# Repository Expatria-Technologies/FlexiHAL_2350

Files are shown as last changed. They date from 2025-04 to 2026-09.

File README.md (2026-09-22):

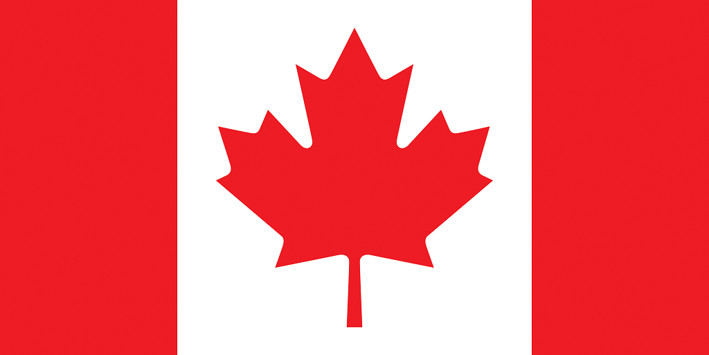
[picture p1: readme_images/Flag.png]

### Canadian-designed open source hardware. For everyone.

# FlexiHAL 2350 CNC Controller
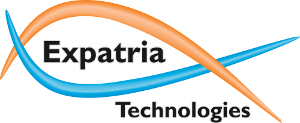
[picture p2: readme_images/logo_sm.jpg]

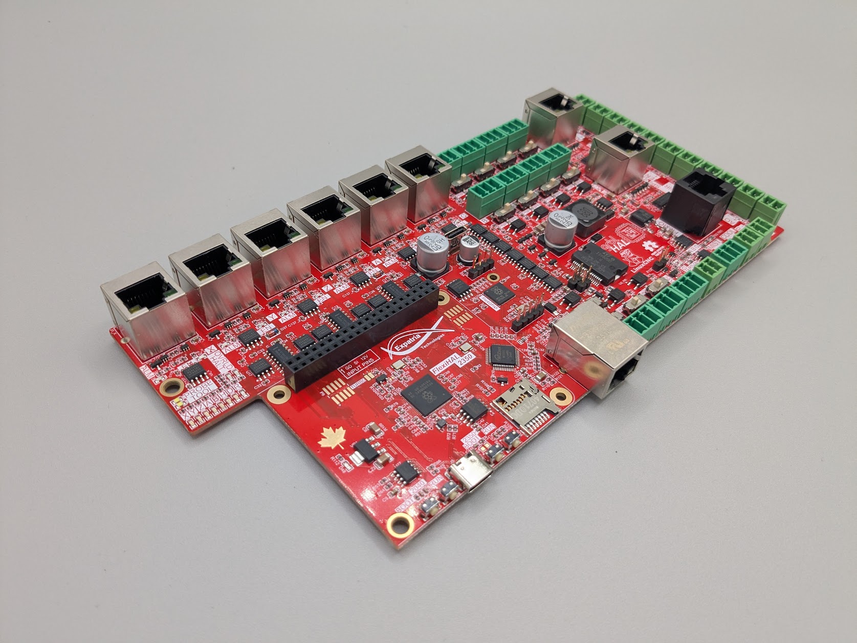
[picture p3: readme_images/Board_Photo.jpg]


Expatria Technologies GRBLHAL and LinuxCNC (and more!) CNC control board

Currently available in our online store:

[https://expatria.myshopify.com/products/flexi-hal-2350](https://expatria.myshopify.com/products/flexihal-2350-cnc-controller-rev-a3-1-for-grblhal-and-linuxcnc)

Please consider buying a board to support our open-source designs. 

The FlexiHal 2350 is designed to be an EMI resistant IO platform for any microcontroller based CNC/motion control firmware or software.  This board includes a few features that we couldn't find on other boards, and it reduces the amount of extra wiring in our setups.  In the co-operative spirit of the PrintNC and other CNC communities, and Open Source Hardware, the FlexiHAL will be licensed and free to use by all parties, including commercial parties, under the CERN-OHL-S V2 license.  It is our hope that the community finds the design useful and that it may be carried forward to help advance the PrintNC and broader CNC hobby community.

The FlexiHAL 2350 is a premium controller that utilizes Raspberry Pi's RP2350 microcontroller.  The RP2350 is well suited for CNC applications using step/direction or quadrature outputs when leveraging the unique capabilities of the PIO cores.    In addition, the Flexi-HAL is intended to be used with the Expatria Real-Time jog controller or similar peripheral:

https://github.com/Expatria-Technologies/RT_Jog_Controller

The key features of the FlexiHAL 2350:

1) 6 Axis of isolated step/dir motor control featuring high-speed digital isolators and differential signal drivers for maximum signal integrity and step rates.
2) 15 general inputs (user+limits+ 2 encoders)
3) 40 points of I/O not including step/dir
4) Integrated support for 3 wire inductive type powered switches.
5) Onboard 5V power regulator.
6) Integrated RS485 with automatic direction control.
7) Support for closed loop stepper motors and servos with alarm feedback.   6 discrete inputs for motor alarm.  6 discrete outputs for motor enable.
8) Two Differential interfaces for a spindle encoder inputs or can be used for general purpose inputs.
9) Real-time control port for remote pendants.
10) Raspberry Pi GPIO connector allows integration of sender software and allows the board to host a full LinuxCNC installation.
11) 5V PWM laser control.  4 additional high-speed 5V outputs.
12) Flood/Mist/Spindle relay drivers.
13) Additional auxilliary relay driver outputs.  8 high-current outputs total.
14) All machine facing IO is galvanically isolated from the MCU and user interfaces.
15) Easy reliable USB-C connection to a PC
16) GRBLHAL Ethernet Websockets or Telnet communication through onboard Ethernet.
17) GRBLHAL SD card G-Code streaming and macro/subroutine storage (including looping and conditional execution) with onboard storage and SD card.

Prebuilt Raspberry Pi LinuxCNC image is located here:  
https://github.com/Expatria-Technologies/Flexi-Pi/releases

Accessory Encoder Breakout PCB is located here:  
[https://github.com/Expatria-Technologies/EST_Accessory_PCB/ENCODER_BREAKOUT_MK2](https://github.com/Expatria-Technologies/EST_Accessory_PCB/tree/main/ENCODER_BREAKOUT_MK2)

Various community mods and accessories are located here:  
https://github.com/Expatria-Technologies/Mods-Accessories

Recommended GRBLHAL Post Processor is here:  
https://github.com/Dietz0r/grblHAL_Fusion360_Post_Processor

## Flexi-HAL Overview

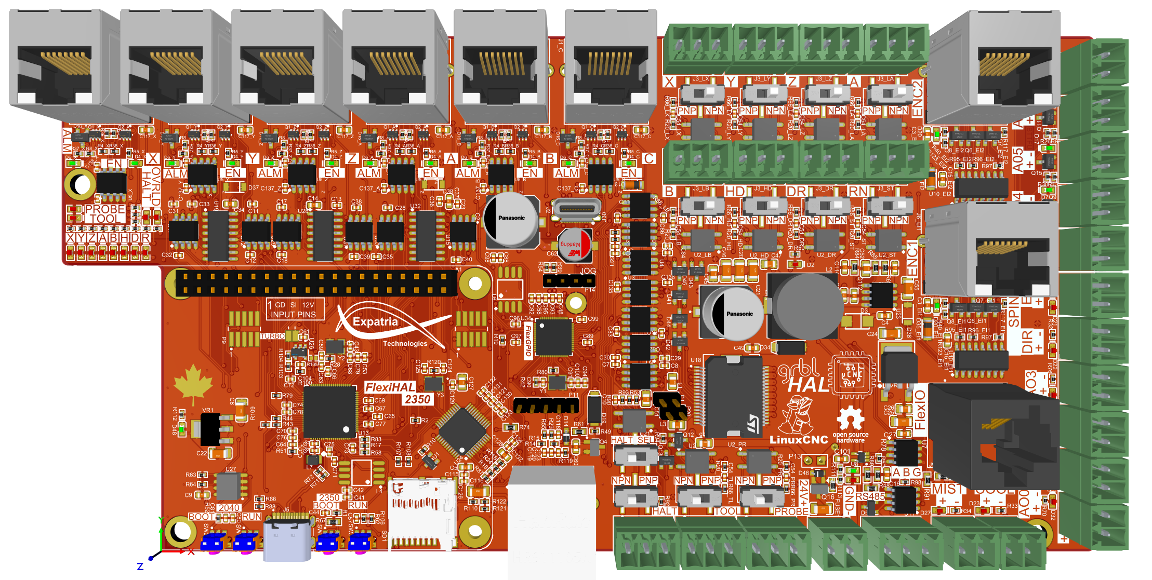
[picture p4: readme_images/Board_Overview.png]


### Pinout List:
This diagram shows which pins connect directly to the RP2350 and which are connected to the RP2040 FlexiGPIO expander.
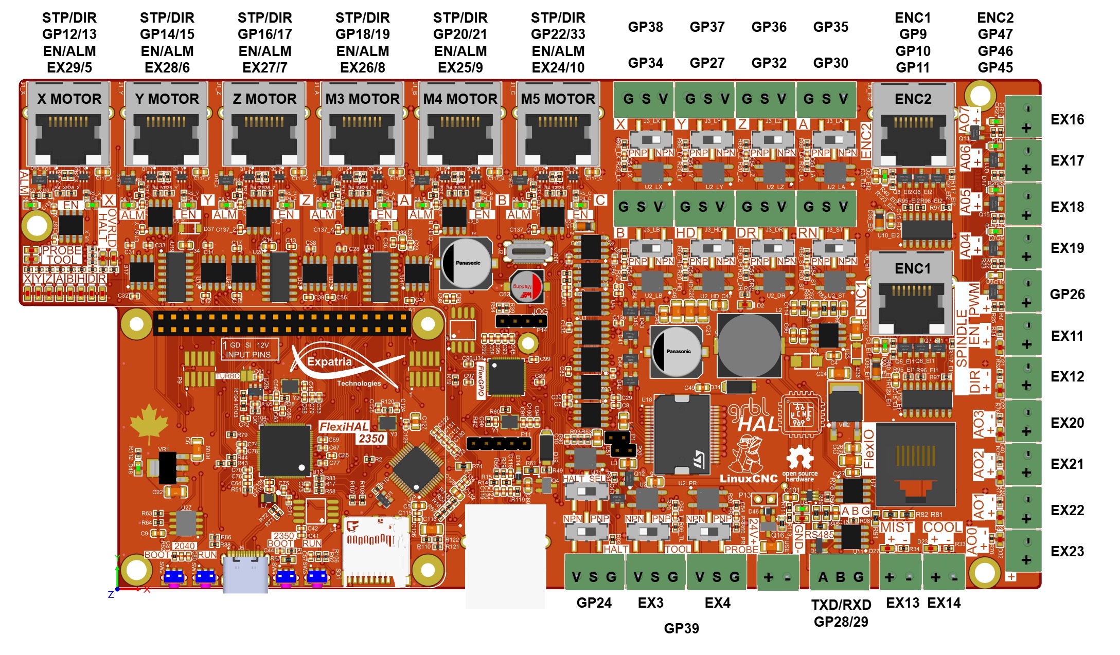
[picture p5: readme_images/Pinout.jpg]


### RP2350 Microcontroller and RP2040 FlexGPIO expander.
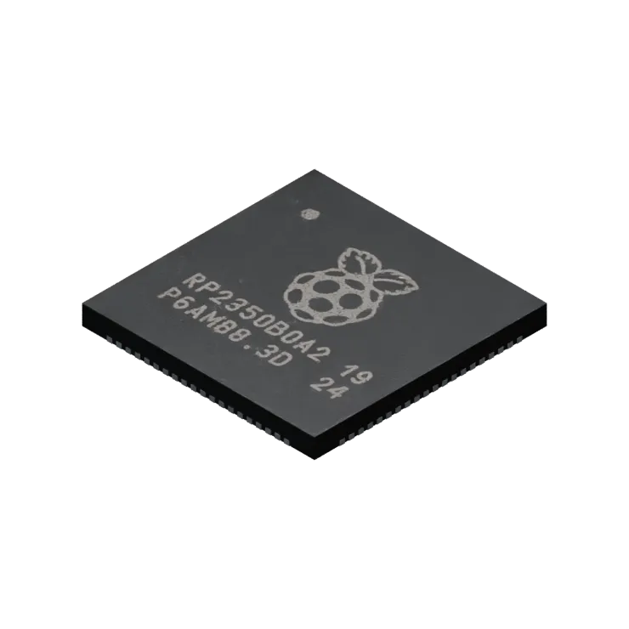
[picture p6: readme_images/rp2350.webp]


The FlexiHAL2350 is built around the RP2350 from Raspberry Pi, an MCU we're genuinely excited about, for its versatile PIO cores and the unique capabilities they unlock.
The board is designed with flexibility at its core, supporting both GRBLHAL and LinuxCNC. In the future we would also like to add support for uCNC.  Pre-built binary firmware for a variety of axis configurations will be made available on the Expatria GitHub, so you can get up and running quickly without compiling from scratch.
For LinuxCNC users, there is a customized port of the Remora project alongside FlexiHAL, making it straightforward to switch between motion control environments. In this mode a Raspberry Pi 5 is recommended when running the Expatria Flexi-Pi image.

In order to expand the amount of I/O available on the board, a custom I2C GPIO expander is implemented on an additional RP2040 MCU.  This allows for a large number of additional IO points with much greater potential flexibility than is offered by traditional GPIO expanders.  It will be possible to implment functions such as additional analog/PWM outputs, nexopixel outputs and additional stepper outputs by extending the FlexiGPIO code.

FlexGPIO source code is posted here:  
[https://github.com/Expatria-Technologies/FlexGPIO](https://github.com/Expatria-Technologies/FlexGPIO)

FlexGPIO GRBLHAL plugin is posted here:  
[https://github.com/Expatria-Technologies/plugin_FlexGPIO](https://github.com/Expatria-Technologies/plugin_FlexGPIO)

### UF2 Bootloader
The FlexiHAL 2350 uses the RP2350's built-in UF2 bootloader. This allows you to upgrade or change the firmware on the flexi as easily as copying a file to a USB drive.  Pre-built binary firmwares from Expatria are distributed as UF2 files.  To enter UF2 mode hold the BOOT button while powering up the board or while pulsing the RUN button.  Note that there are bootloader buttons for both the RP2040 based FlexGPIO expander as well as the main RP2350 processor.

Once in bootloader mode, the Flexi will appear as a USB storage device called "RPI-RP2."  Simply copy the new firwmare to this USB drive and the board will automatically install it and reboot.  Some operating systems may give an error when flashing is complete because the 'disk' was removed without ejecting it.  This error can be ignored.

### Power Input
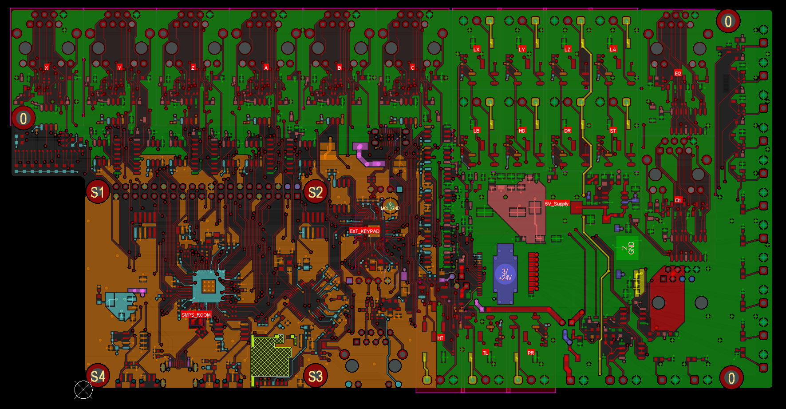
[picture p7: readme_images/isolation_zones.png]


The Flexi-HAL features the capability for full power and ground isolation between the sensitive microncontroller and host circuits, and the external IO that extends out to the rest of the machine.  There is a single input for 12-24VDC.  The board has its own onboard 5V regulator to power the stepper drivers and external RS485 interface.  There is also a small capacity 12V LDO that is specifically for driving the limit and user switches.

Flexi-HAL has reverse polarity as well as over-current protection beyond 1.75A.  This is important to consider when using external relays that draw a lot of current as this may overwhelm the capacity of the board.  If you need to drive more than 250 mA through the auxillary and mist/coolant relay outputs, external relays are likely required.

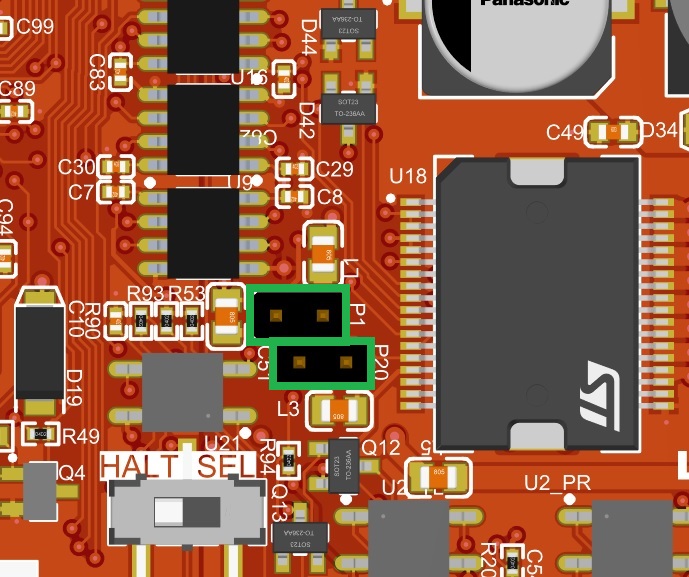
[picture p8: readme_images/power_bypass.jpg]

Normally the MCU and RPI header will be powered via the USBC connector.  The RT control interface is also powered from the isolated domain.  By installing two jumpers on the above offset pins, the 5V power and ground isolation can be bypassed and the Flexi-HAL will operate without an external 5V supply in a semi-isolated state.  This does reduce the EMI resistance of the board and is not recommended when sending Gcode via the USBC connector.

Note: With the isolation jumpers not-populatd, and the Flexi-HAL connected to 12-24v power, it may appear that the board is ready to run as some LEDs illuminate. You MUST provide 5v power to the isolated domain (MCU, Jogger) either through USB or the bypass jumpers in order for the MCU and Jogger to turn on.

### Stepper Drivers
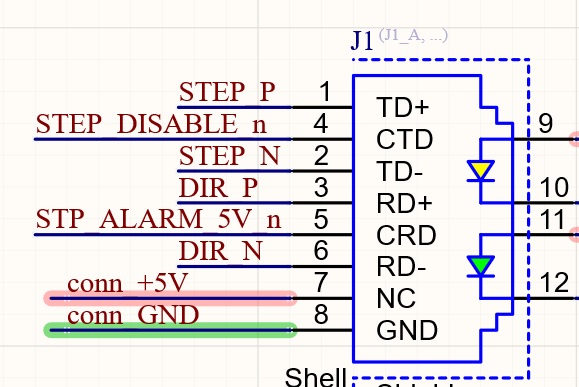
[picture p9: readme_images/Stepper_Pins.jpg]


The stepper drivers are designed to be used with standard or flex rated RJ45 cables.  Unfortunately you will need to ensure that at the external driver the high and low signal pairs are connected correctly as there is no standard pinout on these drivers.  The 8 pin connection allows you to run a high and low pair for every signal to ensure the best possible signal integrity.  The Flexi-HAL uses high speed digital isolators and differential RS-422 style signal drivers for the motion signals.

Dedicated enable and alarm inputs are routed through the FlexGPIO expander.  A specific motor alarm interrupt is provided to immediately notify the host processor.  Alarm and enable can be set to any polarity that is required for operation.  There are LEDs provided on the board for every motor signal to help with debugging wiring issues.

Typical wiring for most open-loop stepper drivers: 



### Auxillary Outputs
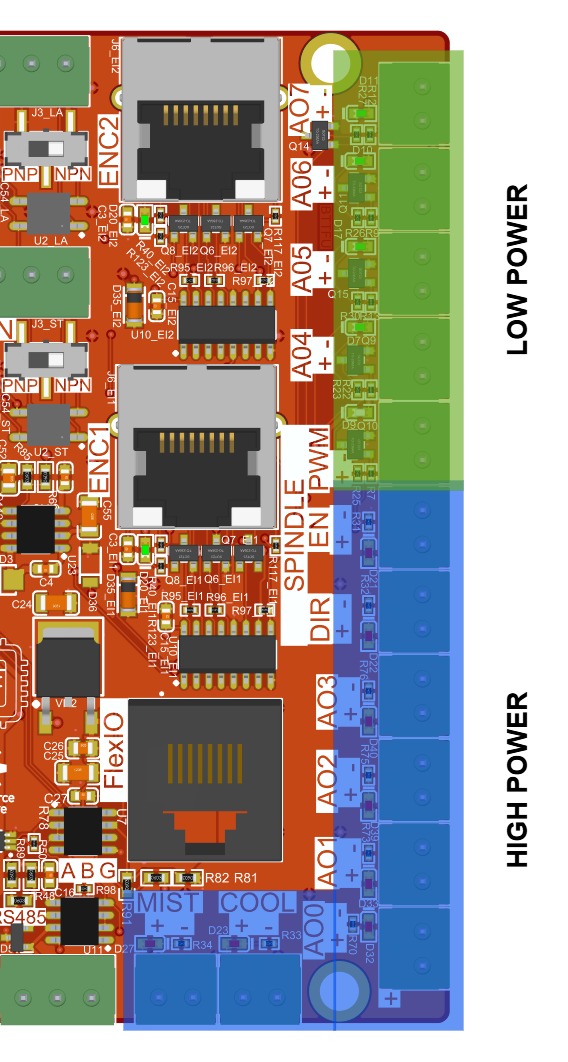
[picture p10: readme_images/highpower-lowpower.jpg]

Two style of outputs are provided: high power and low power.  High power outputs are driven directly from the board input power (12-24V).  Low power outputs are driven at 5V.  All outputs are PNP style high-side switching.

#### High Power Outputs
Any single high-power output can drive up to 700 mA, though the total current supplied by the board is a maximum of 1.75A.  Each automotive grade output has short circuit, over-current and thermal shutdown protection.

#### Low Power Outputs
The low power outputs are designed for fast switching applications such as PWM output, neopixels or even additional stepgens.  They should not be configured to drive more than 10 mA.  They are provided with limited over-voltage and short-circuit protection.

### PWM Spindle Control

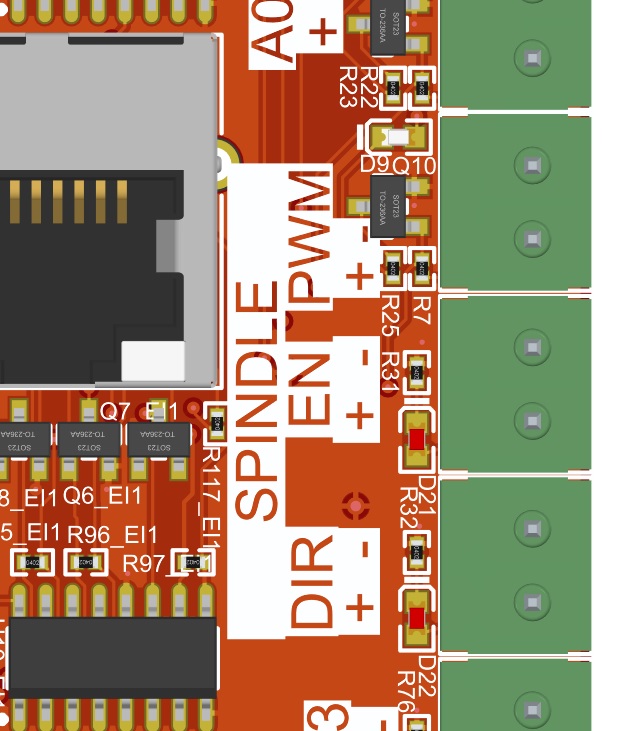
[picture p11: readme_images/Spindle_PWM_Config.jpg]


The spindle PWM pin is directly connected to the RP2350 main MCU.  This is normally used to drive a laser module with pulse modulation.  To use this output with a 0-10V analog spindle control, an external PWM converter must be used.

### RS485 Spindle Control
This interface is primarily intended to be used with a Huanyang style VFD for spindle control.  The A, B and G (common) pins are marked on the top and bottoms sides of the PCB.  Simply connect the appropriate pins to the terminals on the VFD.  Note that the G pin should be used for signal common, it should not be connected to the shield of a shielded cable.

https://github.com/grblHAL/Plugins_spindle/

### 6 Axis limit and auxillary inputs

A total of 9 direct 3 wire opto-coupled inputs are provided to cover limit and auxillary inputs.  Both PNP and NPN switches are supported.  A selector switch is provided on each input.

Auto-squaring is supported by enabling ganged axes in GRBLHAL and setting the appropriate pins.

In addition two probe inputs are provided that are connected to the FlexGPIO with a dedicated interrupt signal.  Polarity and enable masks are fully configurable.

### HALT Input signal and Polarity Selection

The HALT signal is not a safety feature and should not be used in place of a true electrical emergerncy stop.  It is intended to notify the controller of urgent requests.  The halt signal is shared between the PCB terminal and the RT control interface, but the polarity and operation is freely configurable between NPN, PNP, NO and NC.

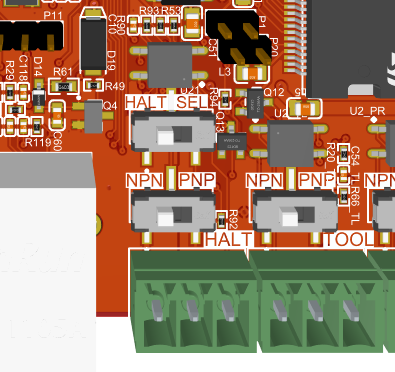
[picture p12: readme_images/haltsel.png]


If you are in doubt of the correct header position for your case, you may simply try both positions and choose the one where the HALT signal is not asserted (red light is not on) when in the nominal operating condition.

### Real-Time Control Port
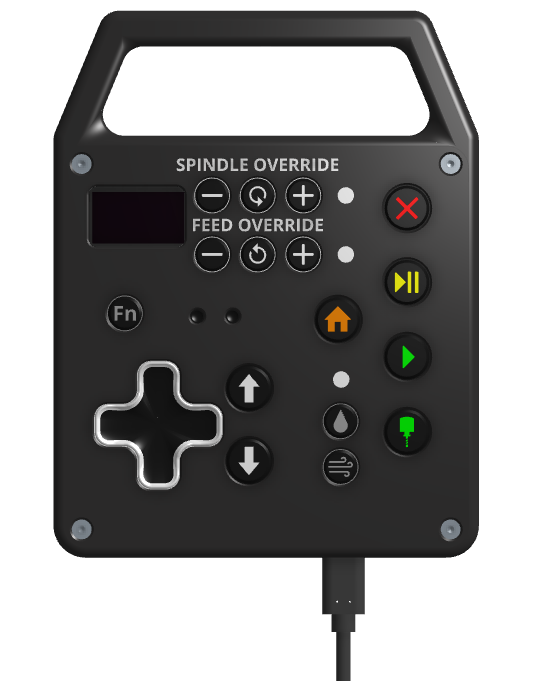
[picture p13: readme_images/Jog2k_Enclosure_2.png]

This port is intended to allow for external pendant type devices to issue real-time jogging and override controls to the motion  controller.  It uses I2C signalling and adds additional signals for the keypad interrupt as well as the Halt signal.  We feel that a robust and wired control is the safest way to interact with a CNC machine in real time.  A simple reference controller implementation is under active development, but there are some additional code examples referenced in the GRBLHAL I2C keypad plugin repository:

https://github.com/grblHAL/Plugin_I2C_keypad/

https://github.com/Expatria-Technologies/RT_Jog_Controller/

### Encoder Input Ports
The two encoder ports are used in either of two ways.  First, these ports allow a differential connection to an external encoder for a robust GRBLHAL lathe implementation or to support a high-speed encoder input for LinuxCNC.  An encoder such as E6B2-CWZ1X is suitable for most spindle applications.  Additionally, an encoder based isolated ADC module can be used for Plasma THC applications.

The RJ45 pinout:  
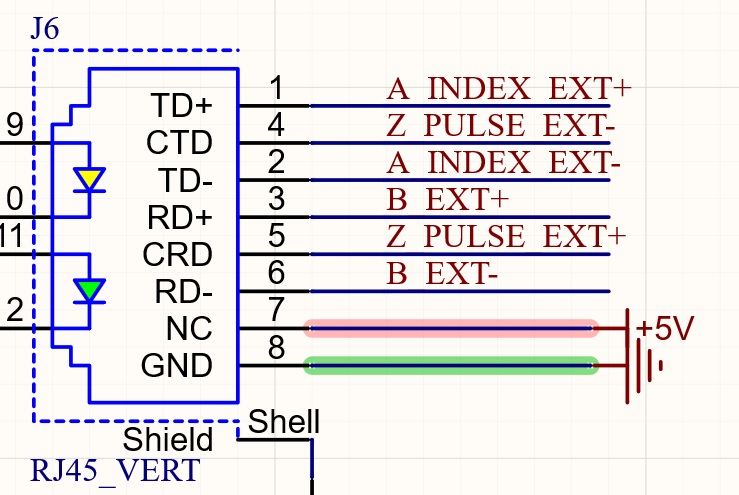
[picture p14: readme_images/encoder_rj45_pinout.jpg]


There is also a small breakout available that exposes these signals for use as discrete opto-coupled inputs.  This can be useful when you have a group of signals that are remotely co-located (such as the sensors in an ATC spindle) so that you only need to bring one cable back to the mainboard.

Encoder Breakout Board:  
[https://github.com/Expatria-Technologies/EST_Accessory_PCB/tree/main/ENCODER_BREAKOUT_MK2](https://github.com/Expatria-Technologies/EST_Accessory_PCB/tree/main/ENCODER_BREAKOUT_MK2)
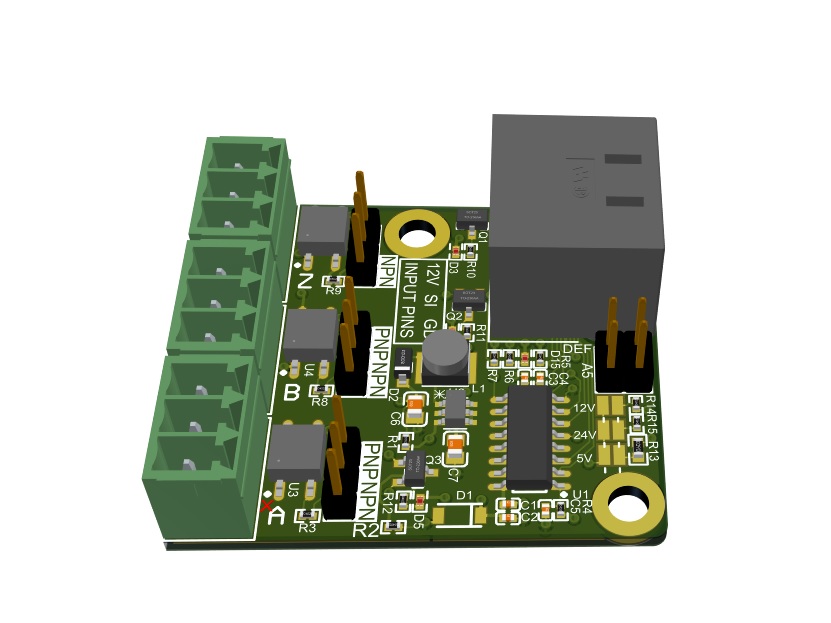
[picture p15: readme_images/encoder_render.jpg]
  

### FlexIO Port
The FlexiHAL2350 introduces a new type of expansion port for Expatria.  The FlexIO port multiplexes the RS485 interface independently to a second connector that carries both power and RS485 signals.  This can be used as both a power source for external modules that are powered from the FlexiHAL's 24V input, or it can serve as a power supply for the board.  The RS485 signalling can be used with Modbus server devices such as the PicoHAL running the nanoModbus GRBLHAL plugin to provide independent control of toolchanges, LEDs, fans etc.

The RJ45 pinout:  
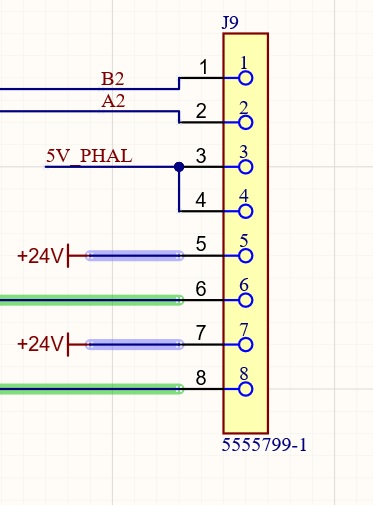
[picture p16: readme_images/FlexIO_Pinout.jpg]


Details on the PicoHAL are posted here:  
[https://github.com/Expatria-Technologies/PicoHAL_HW](https://github.com/Expatria-Technologies/PicoHAL_HW)

NanoModbus GRBLHAL Plugin is posted here:  
[https://github.com/Expatria-Technologies/grblhal_nmbs_plugin](https://github.com/Expatria-Technologies/grblhal_nmbs_plugin)

nanoModbus toolchanger in action; also showing Sienci's ATCI plugin.  In this video, the LEDs and all motions of the tool carousel are controlled via RS485 Modbus.

https://github.com/user-attachments/assets/e5c6b0d1-849d-4eac-88a9-3914cdb023e6

### Raspberry PI expansion header
The Rasberry Pi GPIO header allows the Flexi-HAL to host a full Raspberry Pi type SBC.  This allows the platform to support LinuxCNC via the Remora project.  Power should be connected to either the Pi or to the FlexiHAL, not both.

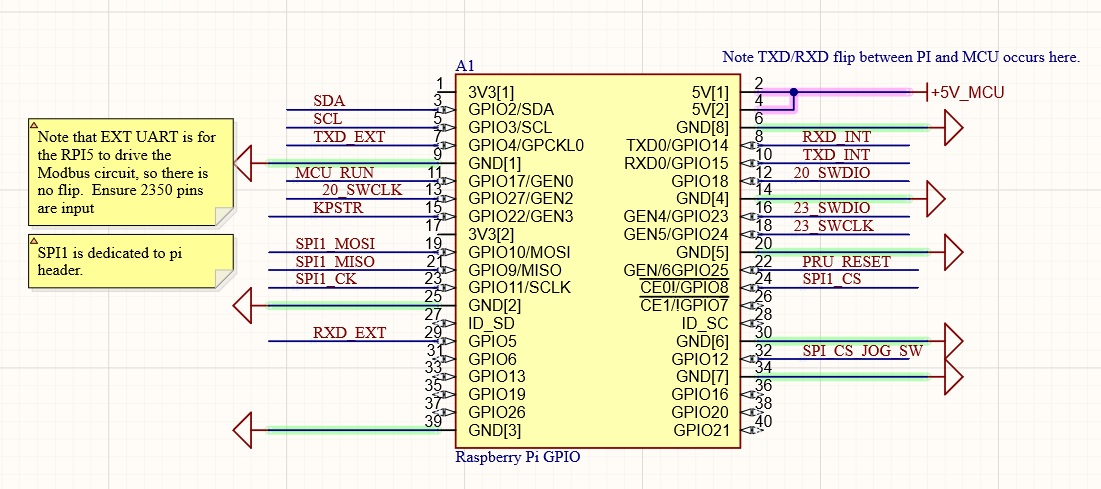
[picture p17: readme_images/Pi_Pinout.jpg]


### Accessories
Some 3D printed accessories are avilable in [Mods & Accessories](https://github.com/Expatria-Technologies/Mods-Accessories/), including a DIN rail mount and enclosures/mounts for the limit and button breakouts.

### Default Jumper Locations
There are no jumpers needed for the operation of this board.  The only jumpers are for the 5V power bypass.

### Example Wiring Diagram
A comprehensive wiring diagram has been developed by the PrintNC community using the FlexiHAL.  While not specific to Flexi, this gives a great example of how to connect the board into the rest of a complete electronics box to drive a CNC machine. 
https://wiki.printnc.info/en/v3/wiring

### Attributions
This project uses components from the very helpful actiBMS library.

https://github.com/actiBMS/JLCSMT_LIB

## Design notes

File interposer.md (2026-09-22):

For the A3 beta release of the FlexiHAL2350, an interposer is necesssary to use LinuxCNC via SPI to a Raspberry Pi 5.  If you purchased a beta board before June 5 2026 and did not receive an interposer, please contact Expatria via the webstore or on Discord and we will send you one.

The interposer doubles as a GPIO extender to allow use of an RPI5 with the OEM heatsink/cooler.  To install the interposer, make sure the white stripe is towards the RPI5 area of the board (pointed at the RP2350) as shown in the images below.

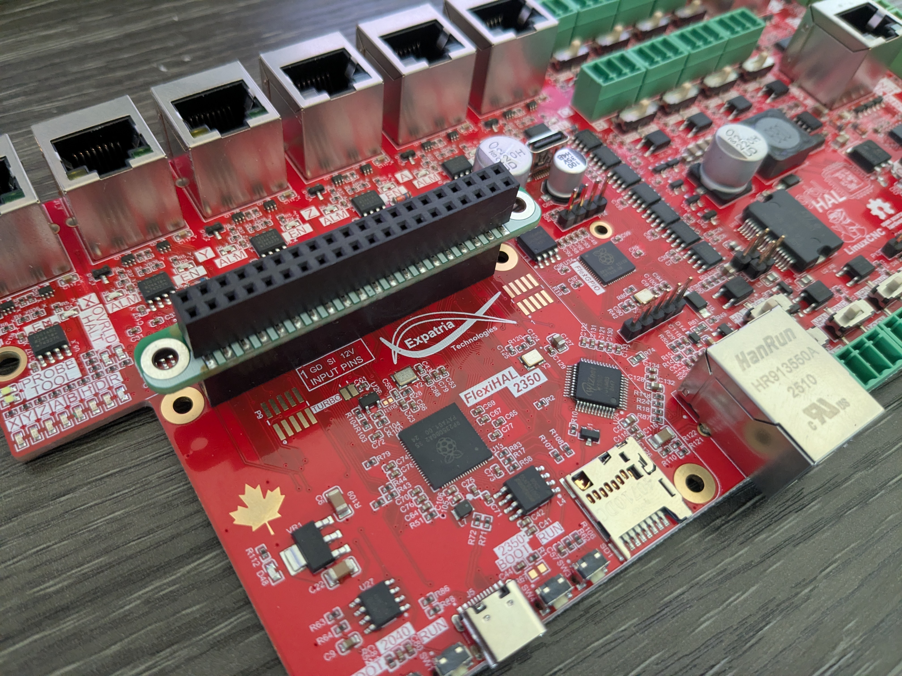
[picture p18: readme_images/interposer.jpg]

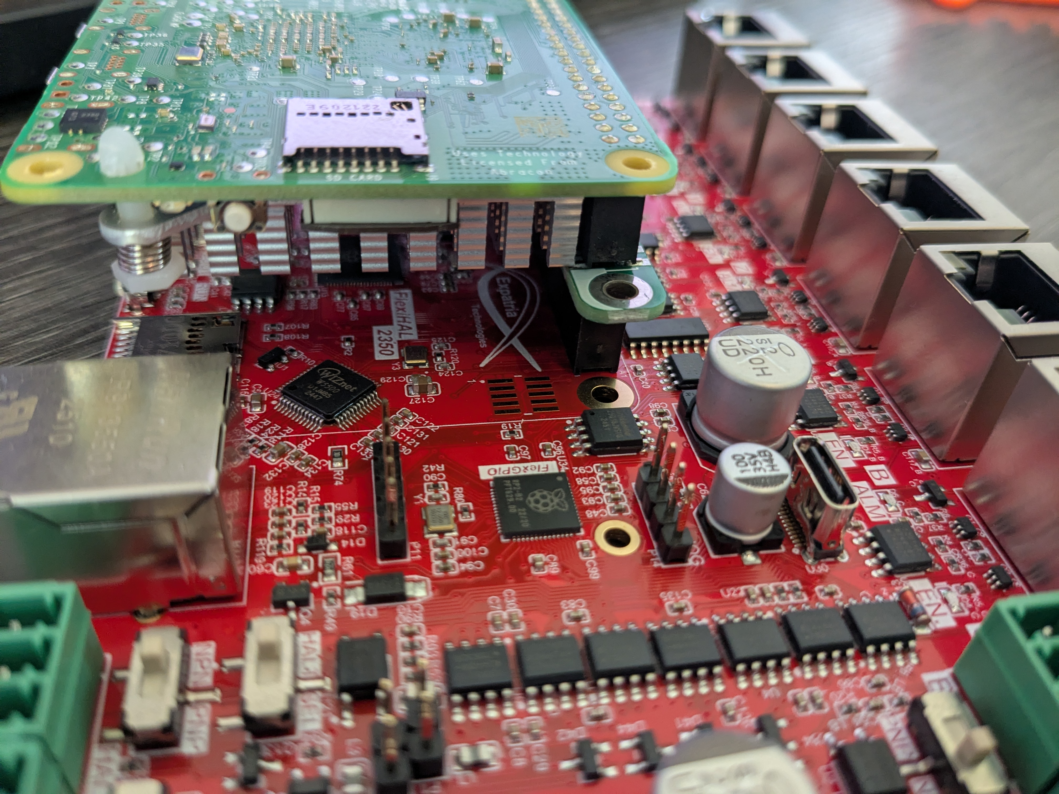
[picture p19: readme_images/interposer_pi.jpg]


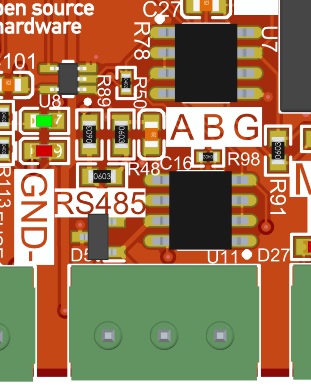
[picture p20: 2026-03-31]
readme_images/RS485_secion.jpg

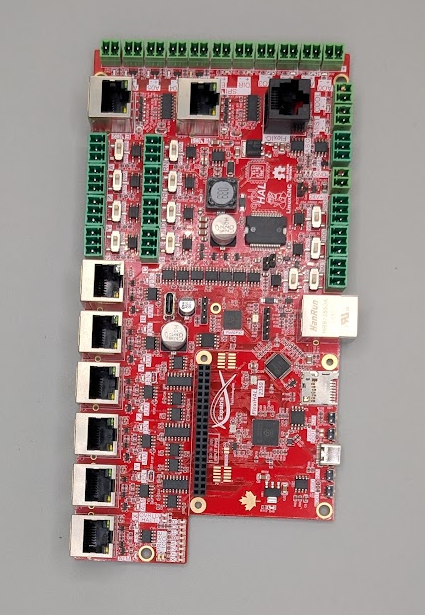
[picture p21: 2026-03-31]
readme_images/board_top.png

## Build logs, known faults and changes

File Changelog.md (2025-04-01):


# Flexi-HAL CNC Controller

## Changelog

### A4 Revision

- Initial Release

### A5 Revision
- Added HALT signal polarity selection.
- Modified RS485 UART isolation for better compatibility with more VFDs under LinuxCNC.
- Added jumper resistor option to route STP_ALARM signal to B limit switch input.
- Depopoulated isolation bypass headers to prevent magic smoke escape.
- Added termination resistors to encoder input to improve signal integrity.
- Added additional overvoltage protection to external circuits.

- ### A6 Revision
- Fixed silkscreen issue on Probe and Tool ports.
- Updated silkscreen to clarify copyright permissions on Expatria and FlexiHAL names.
- Added solder points to USB nets on top layer.
- Changed encoder routing for better signal integrity.  Pinout is unchanged.

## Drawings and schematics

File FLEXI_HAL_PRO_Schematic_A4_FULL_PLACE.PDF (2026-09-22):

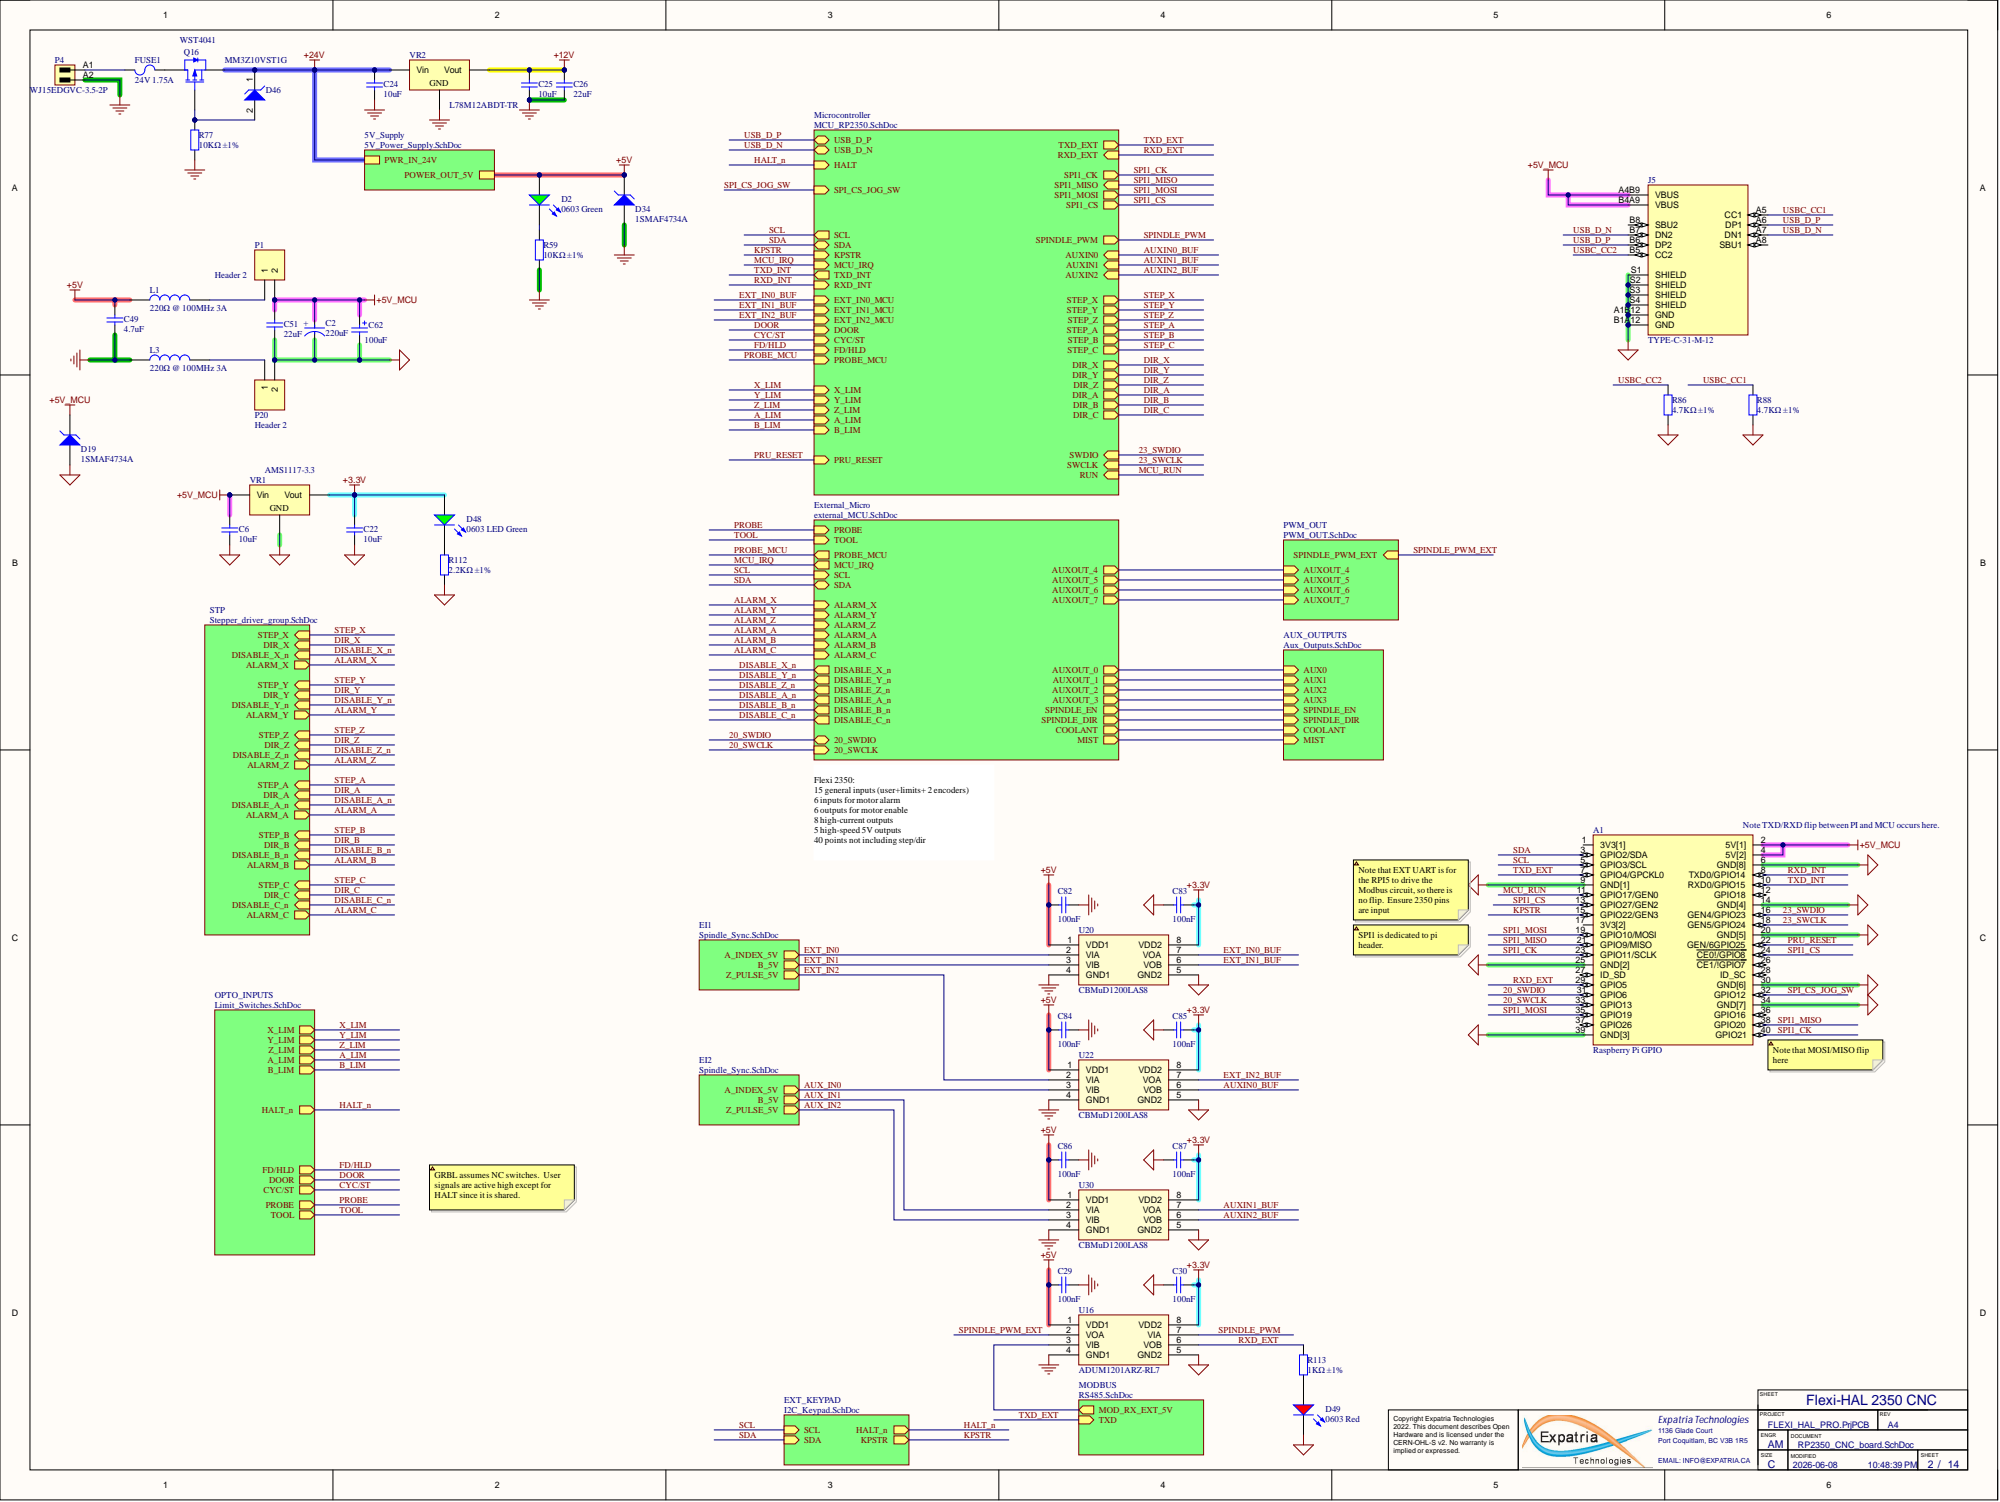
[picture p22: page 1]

hat MOSI/MISO fl

Hardware a n d i s l i c e n s e d u n d er th e CERN-OHL-S v 2. No warra nty i s i m p l i e d or e x pre s s e d . | | P R OJE C T FLEXI_HAL_PRO. P rj P C | R E V A4

B Copyright Expatria Technologies 2022. This document describes Open

E N G R A M | D O C U M E N T RP2350_C N C_board. S c h D o c

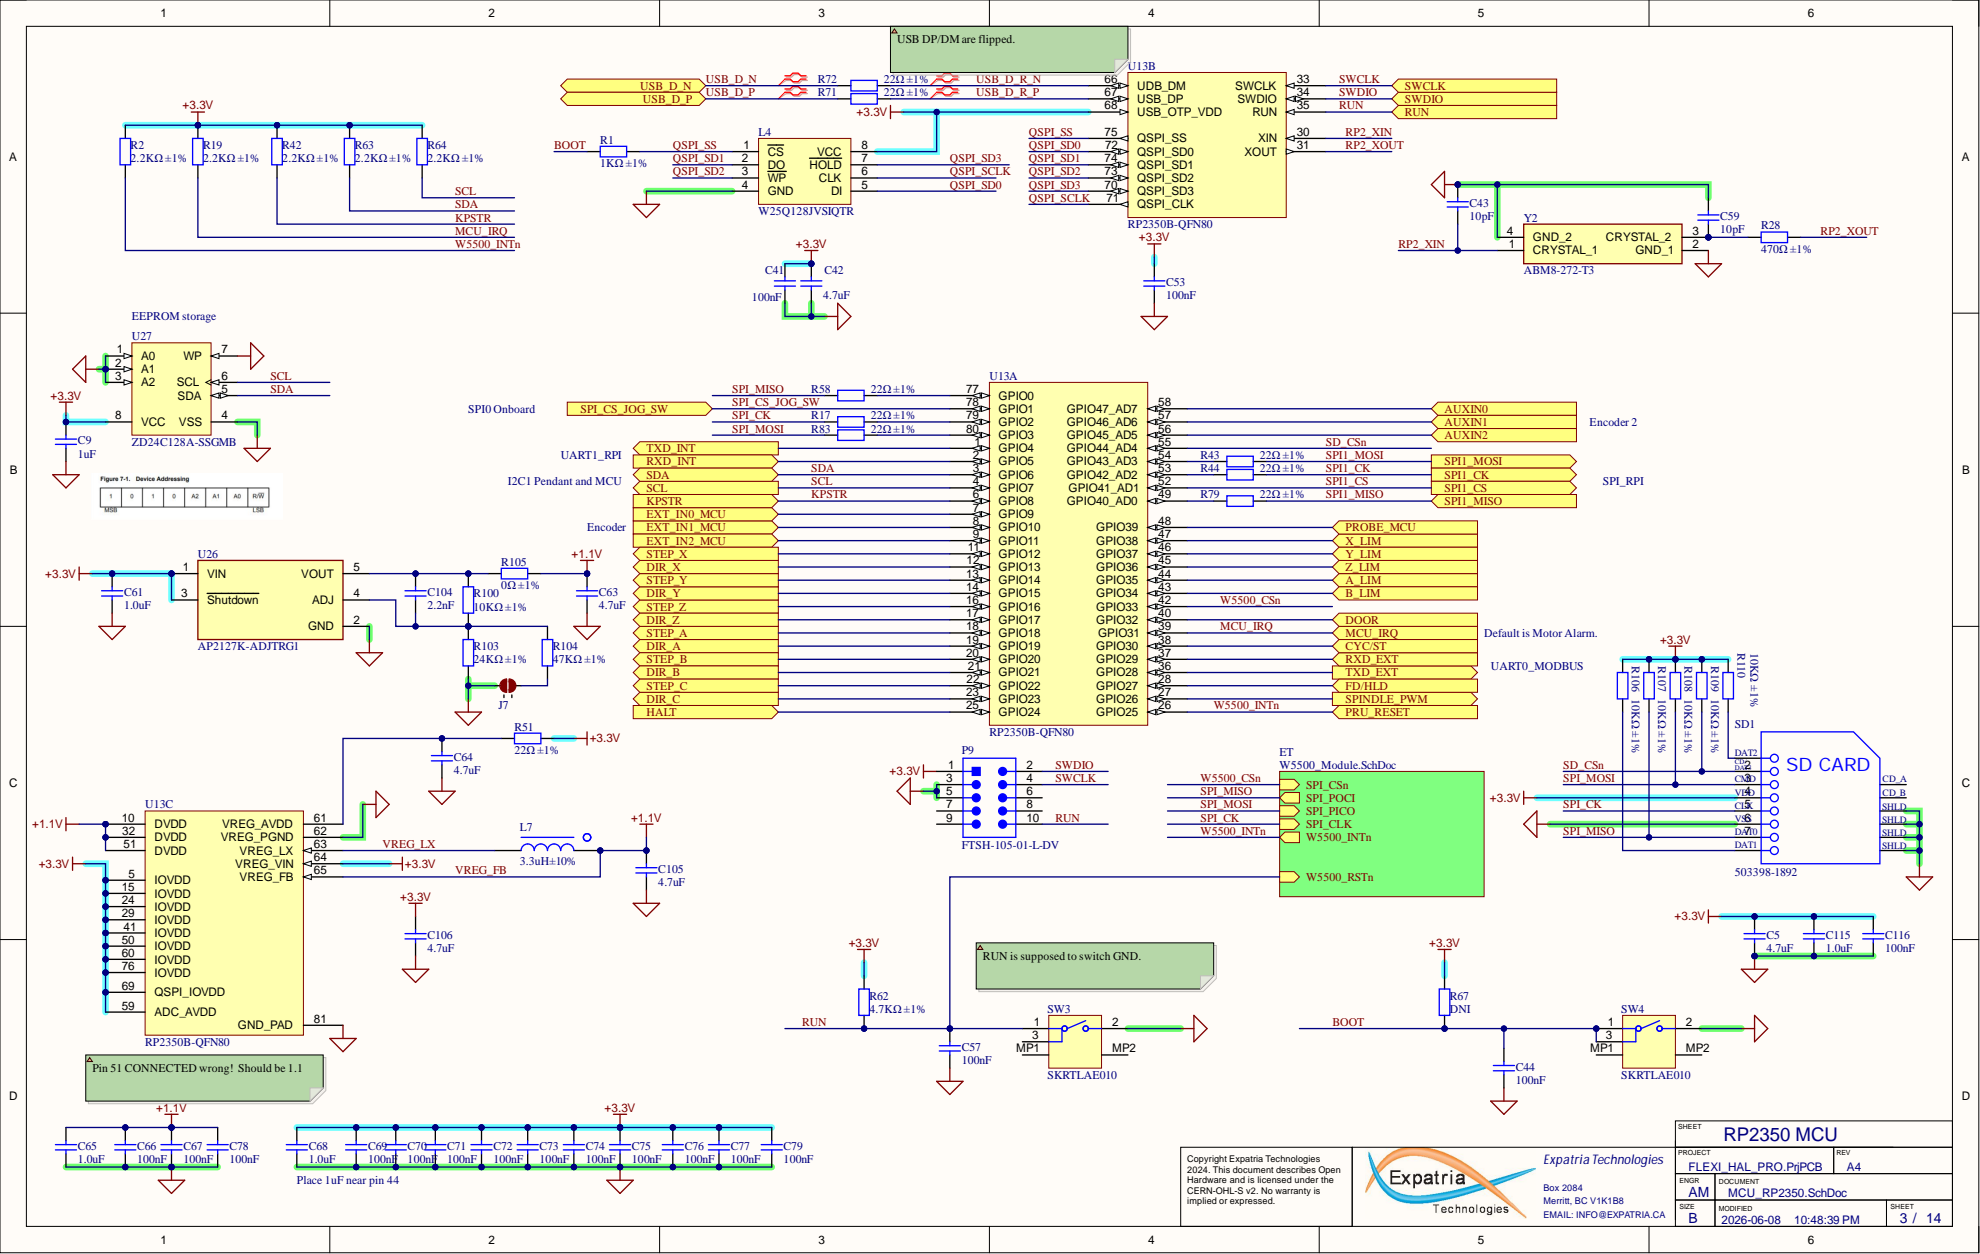
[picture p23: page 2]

USB DP/DM are flipped.

RUN is supposed to switch GND.

Pin 51 CONNECTED wrong! Should be 1.1

Copyright Expatria Technologies 2024. This document describes Open Hardware and is licensed under the CERN-OHL-S v2. No warranty is implied or expressed. | | PROJECT FLEXI_HAL_PRO.PrjPCB | REV

AM ENGR | DOCUMENT MCU_RP2350.SchDoc

Box 2084
Merritt, BC V1K1B8
EMAIL: INFO@EXPATRIA.CA

SIZE B | MODIFIED 2026-06-08 10:48:39 PM | SHEET

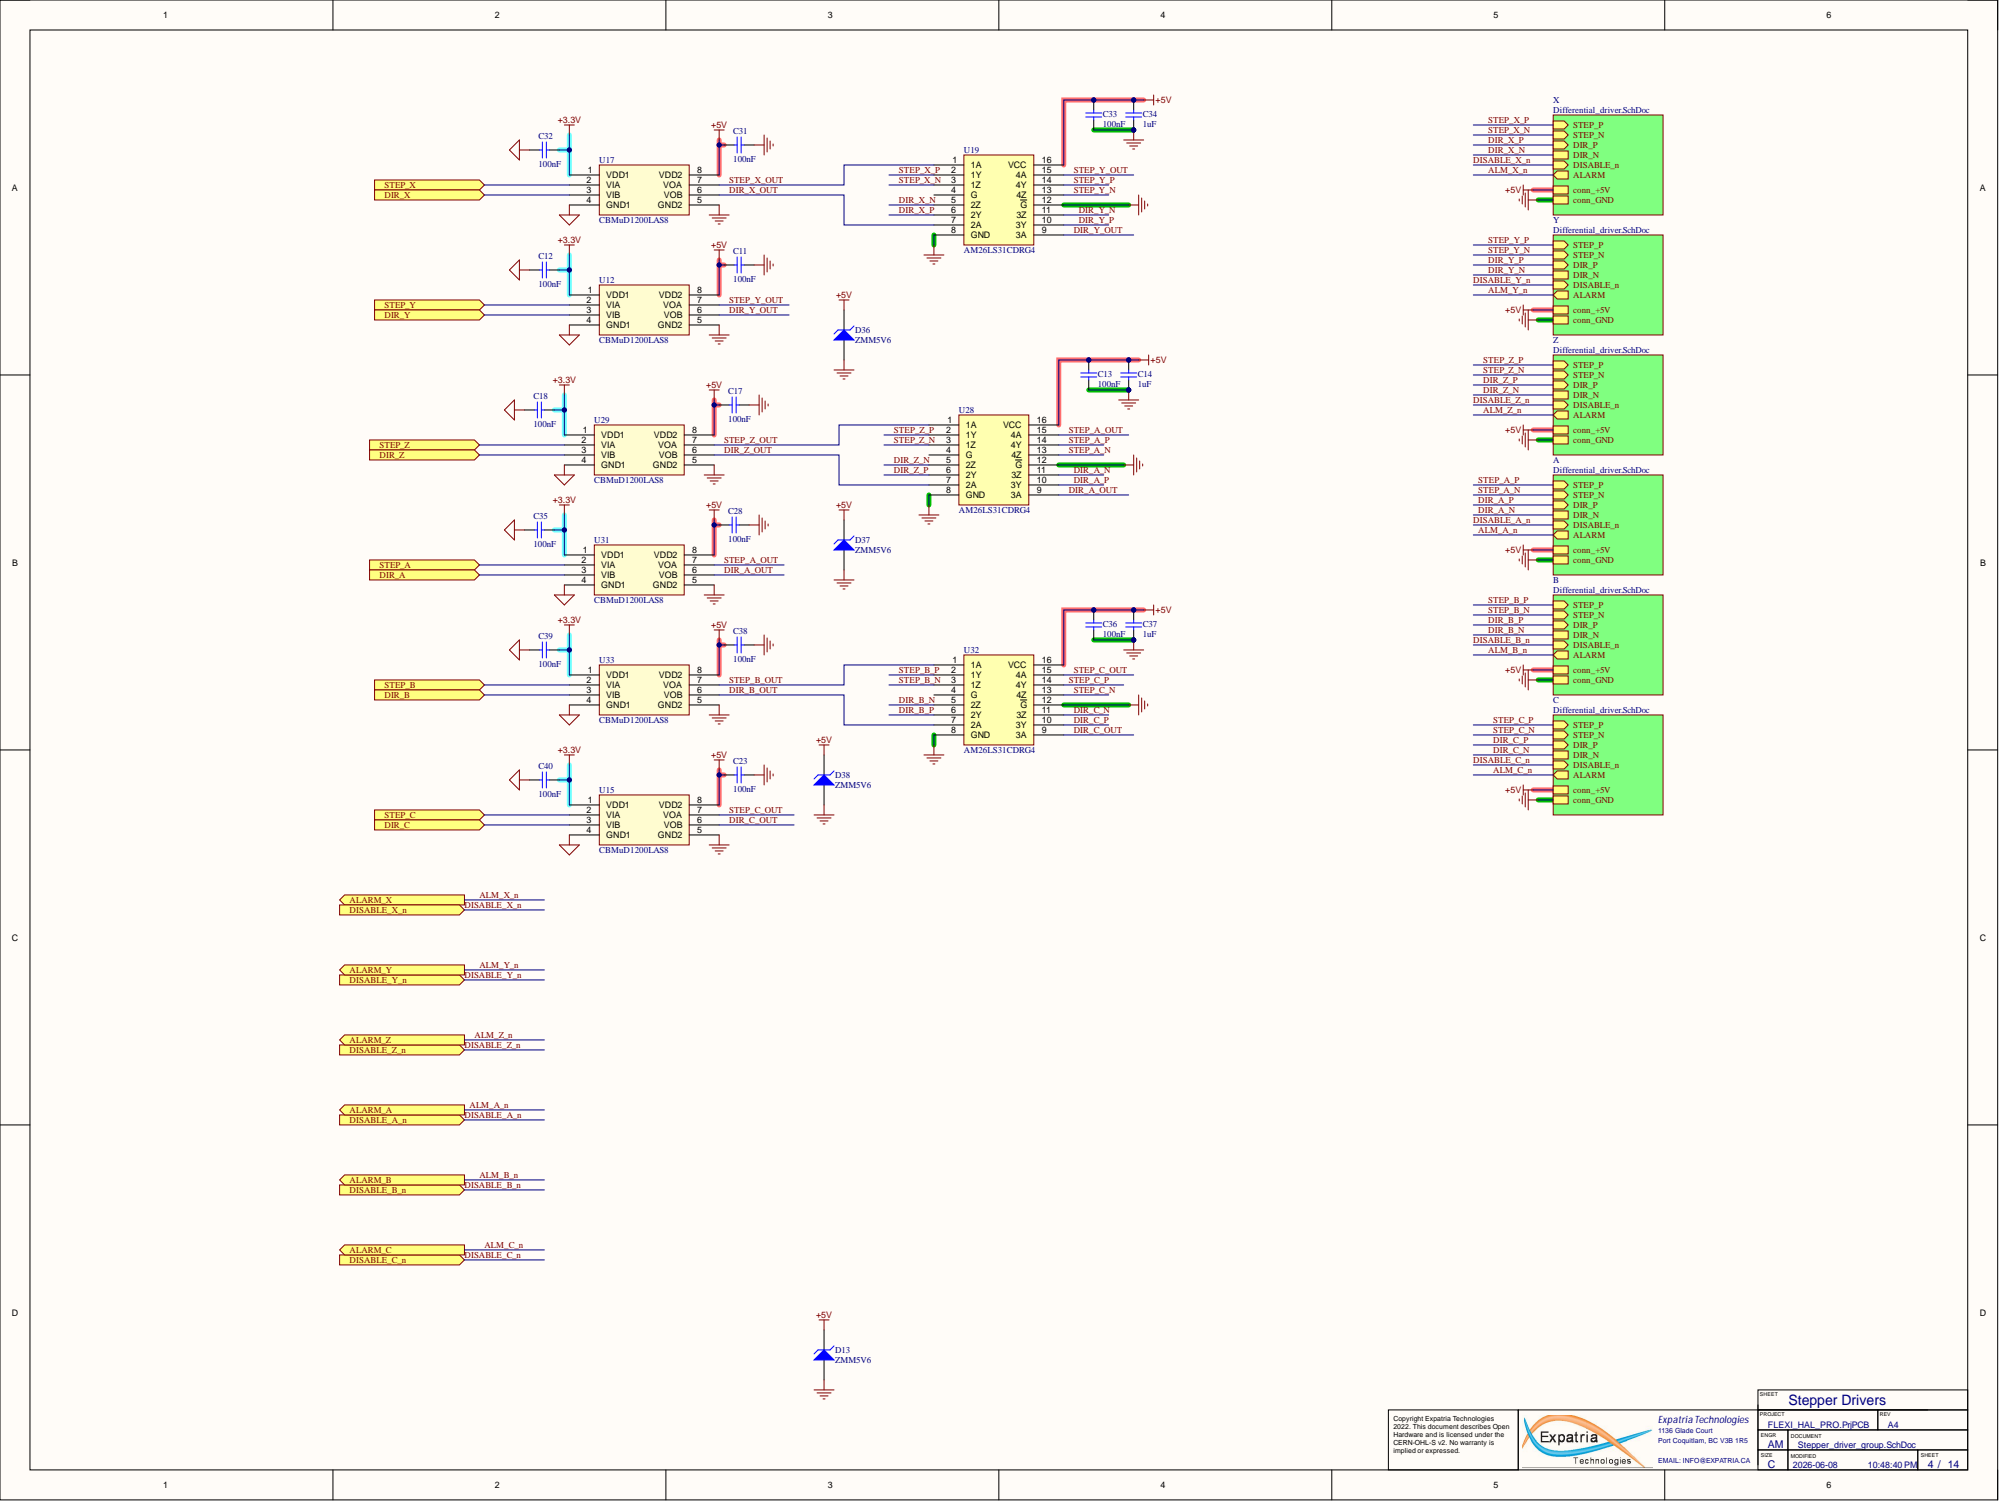
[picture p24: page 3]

FLEXI_HAL_PRO.PrjPCB Copyright Expatria Technologies

ENGR AM | DOCUMENT Stepper_driver_group.SchDoc

implied or expressed.

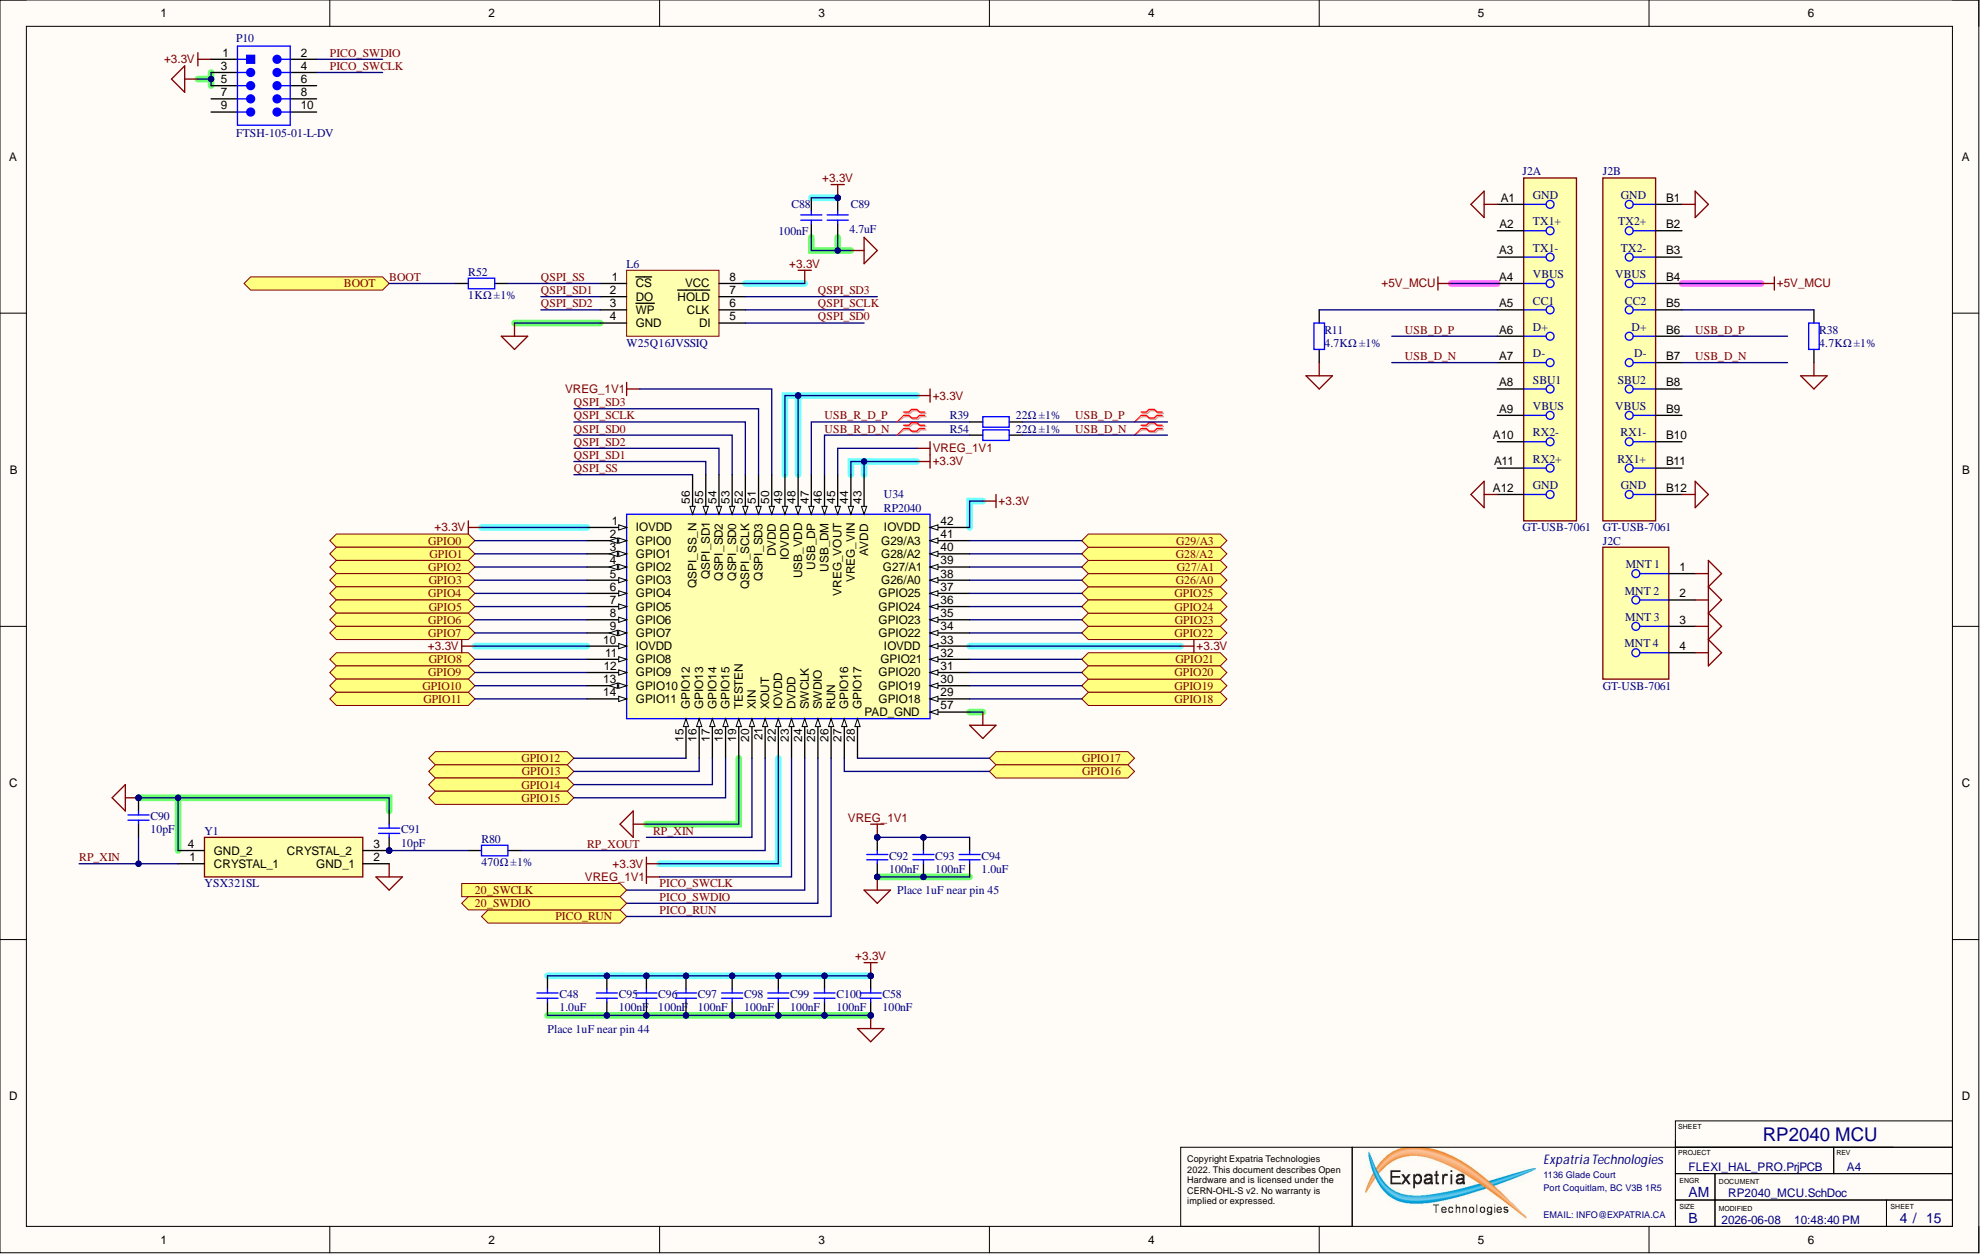
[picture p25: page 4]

QSPI_SD2
QSPI_SD1
QSPI_SS

RP_XOUT R80

RP2040_MCU.SchDoc

RSTn 37 RSVD 38 RSVD 39 RSVD 40 RSVD 41 RSVD 42 PMODE2 43 PMODE1 44 PMODE0 45 NC 46 NC 47 AGND 48

SPDLED 24 LINKLED 25 DUPLED 26 ACTLED 27 VDD 28 GND 29 XI/CLCKIN 30 XO 31 SCSn 32 SCLK 33 MISO 34 MOSI 35 INTn 36

TX_R_P | | TXP 2

AGND 3 | SPI_POCI
AVDD 4

RX_R_P | RXP 6 | XO

DNC 7 | XI

AGND 9
EXRES1 10
AVDD 11 | GRN_LED

W5500_Module.SchDoc

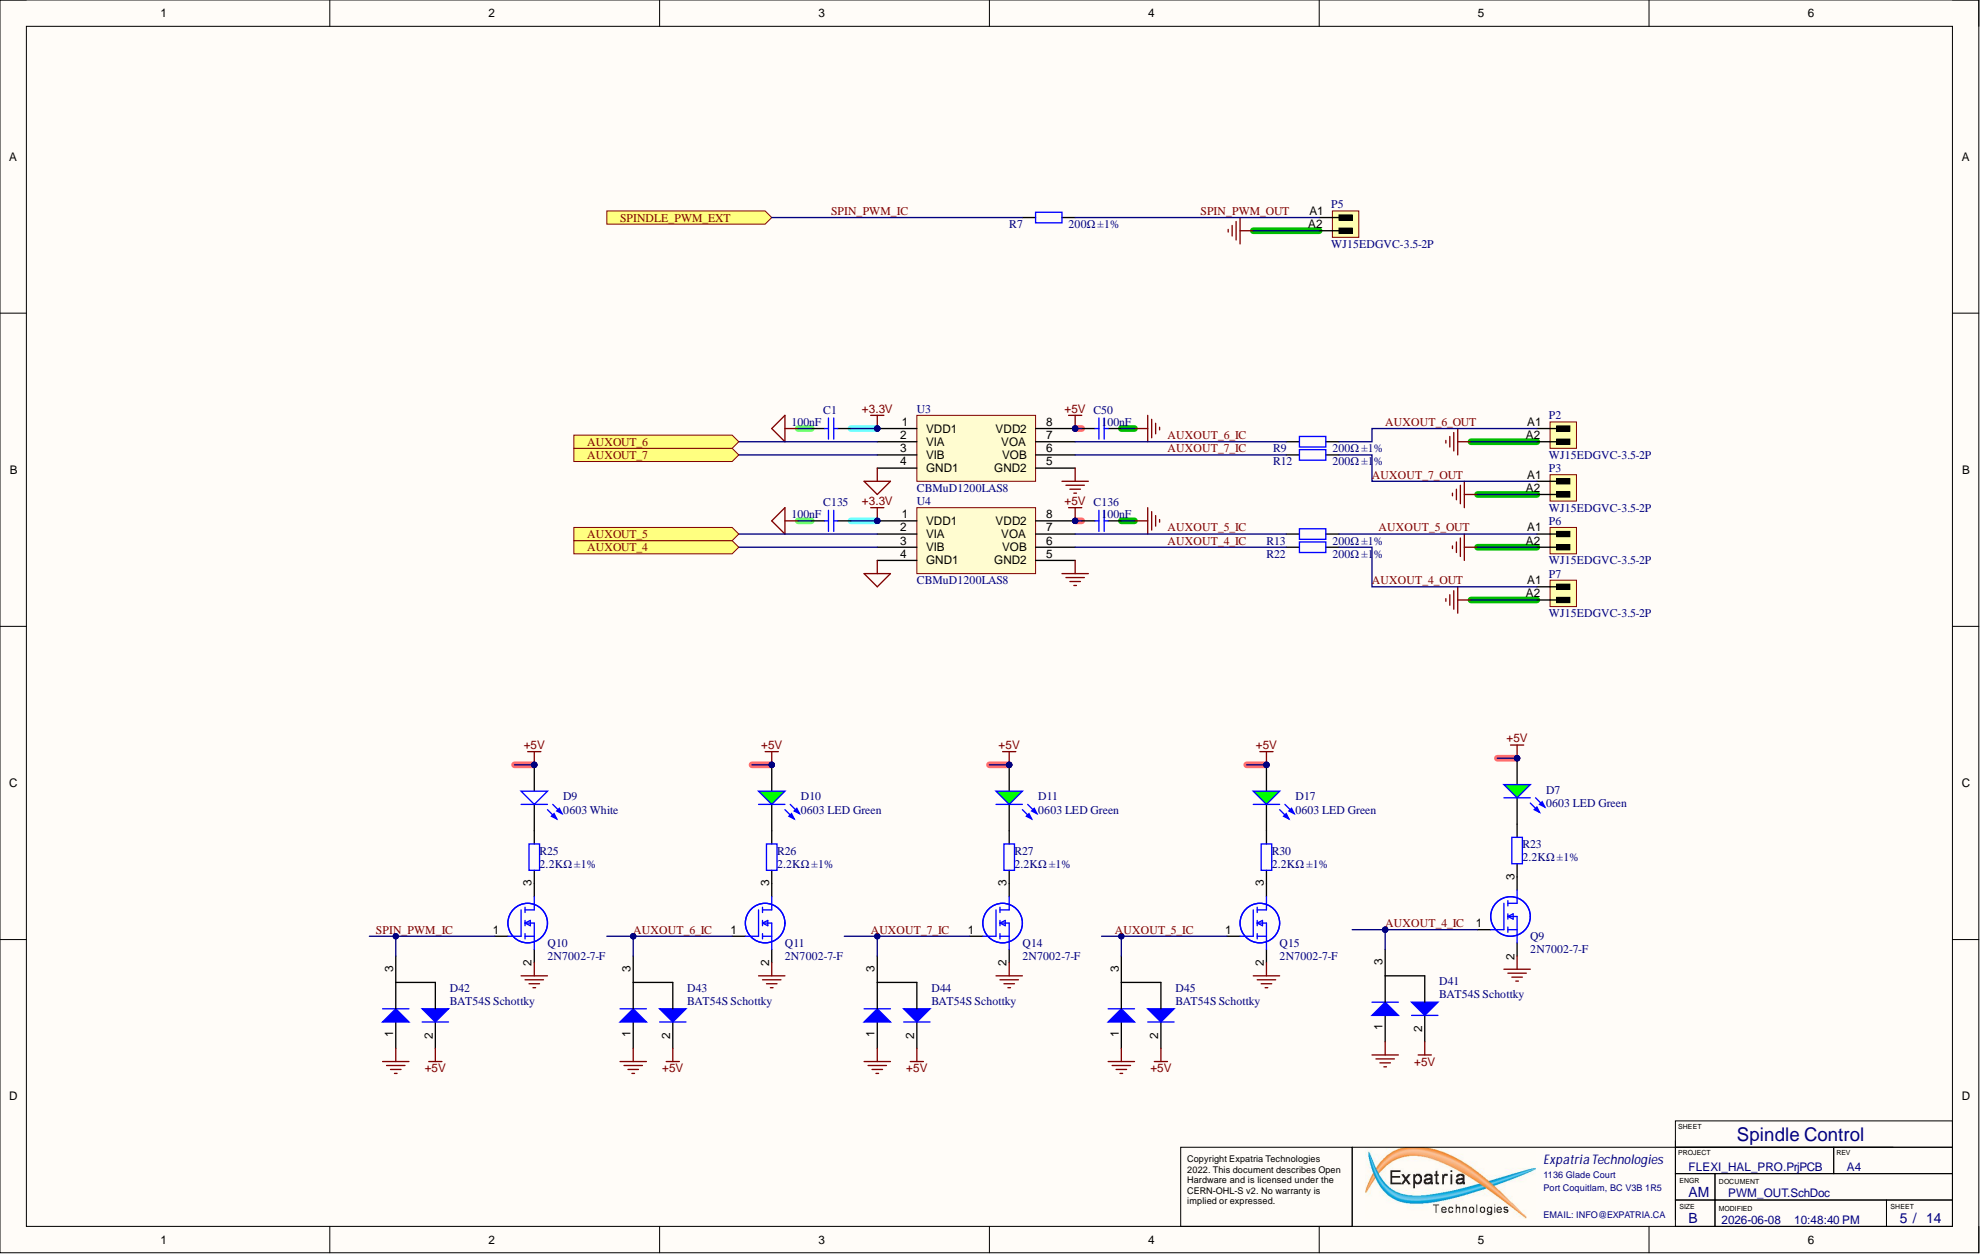
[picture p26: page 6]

PWM_OUT.SchDoc

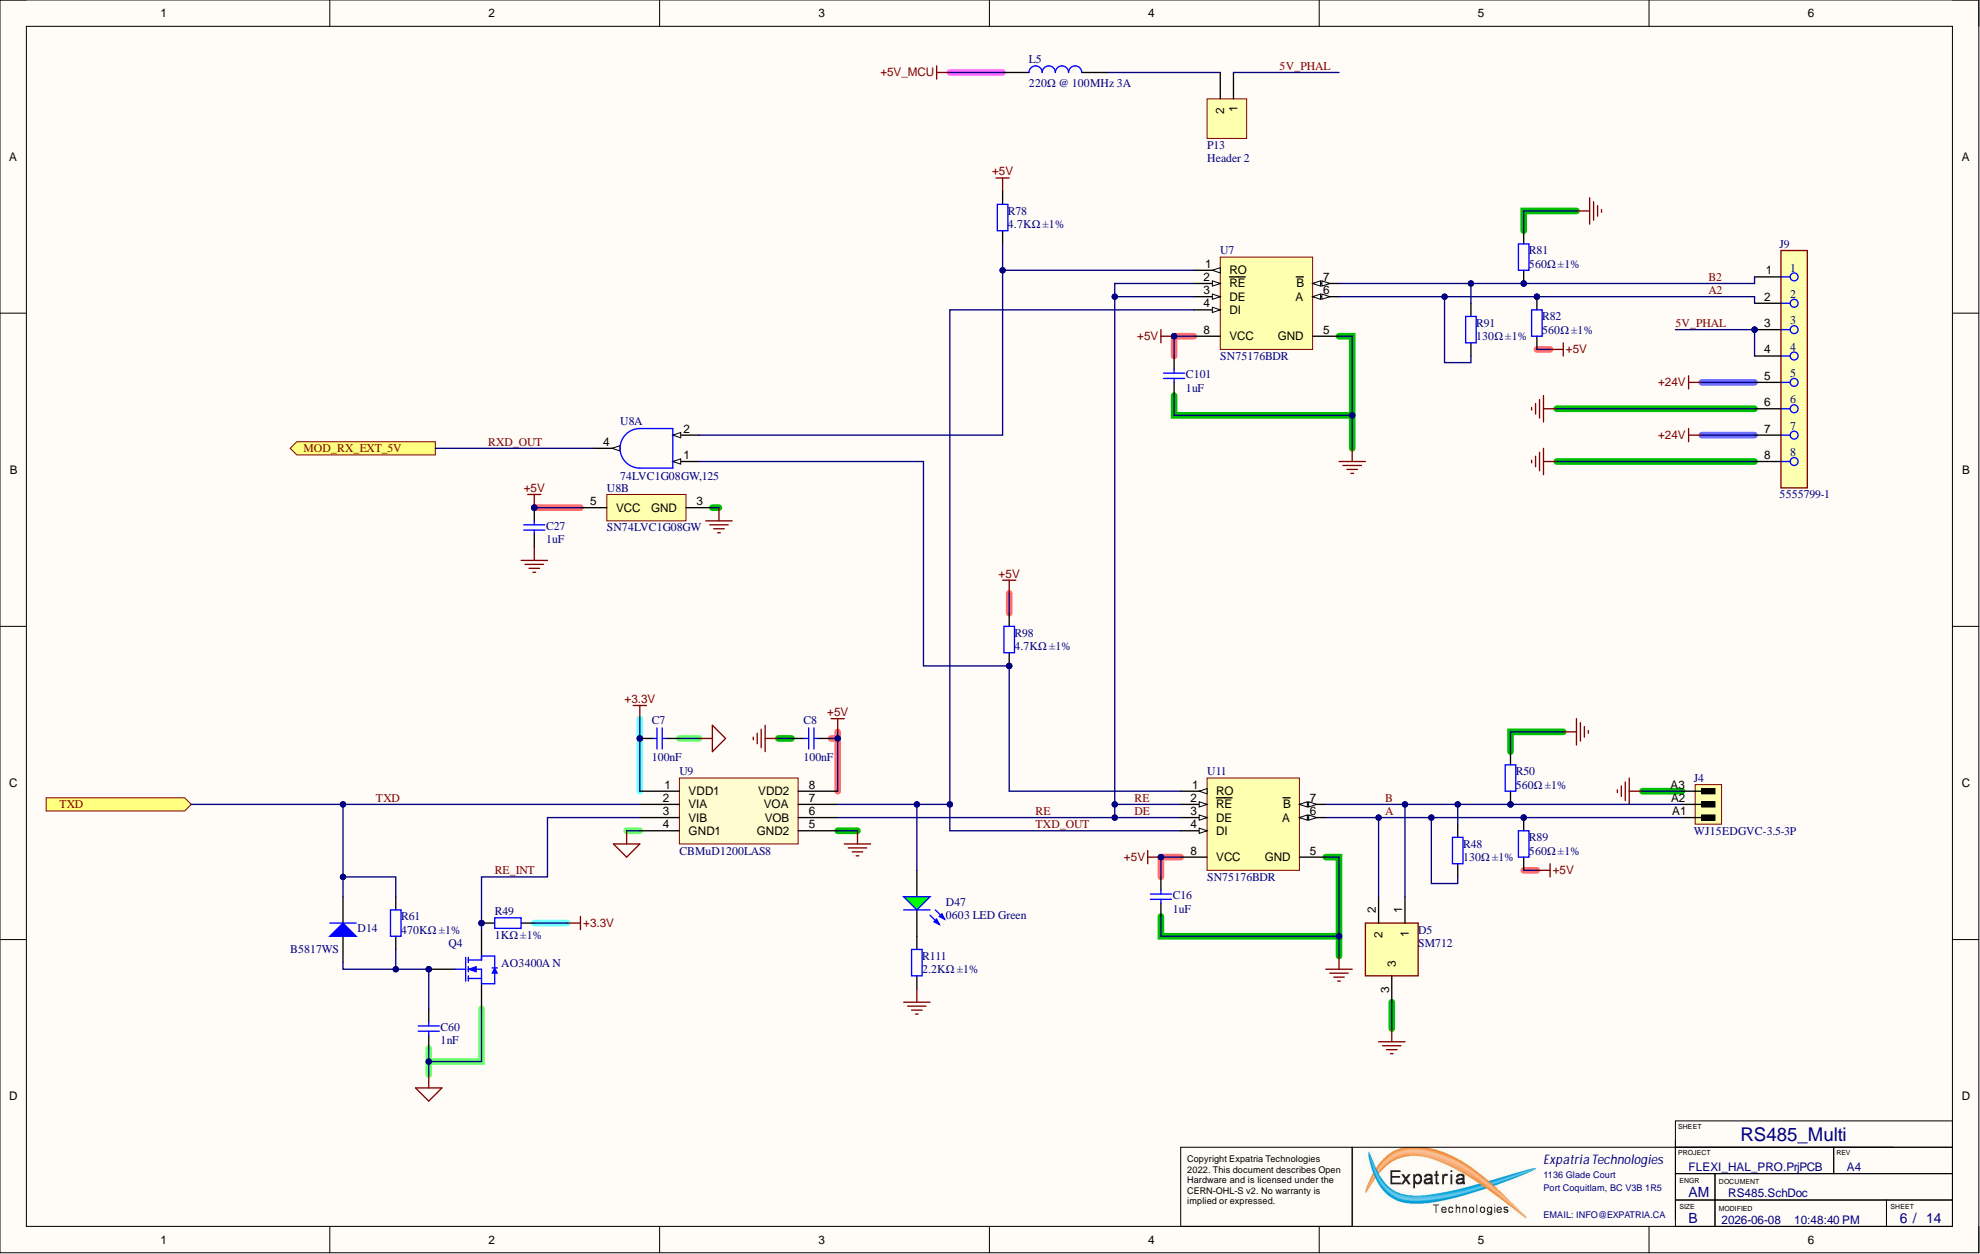
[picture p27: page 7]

RE 2
DE 3 | A2
DI 4

RS485.SchDoc

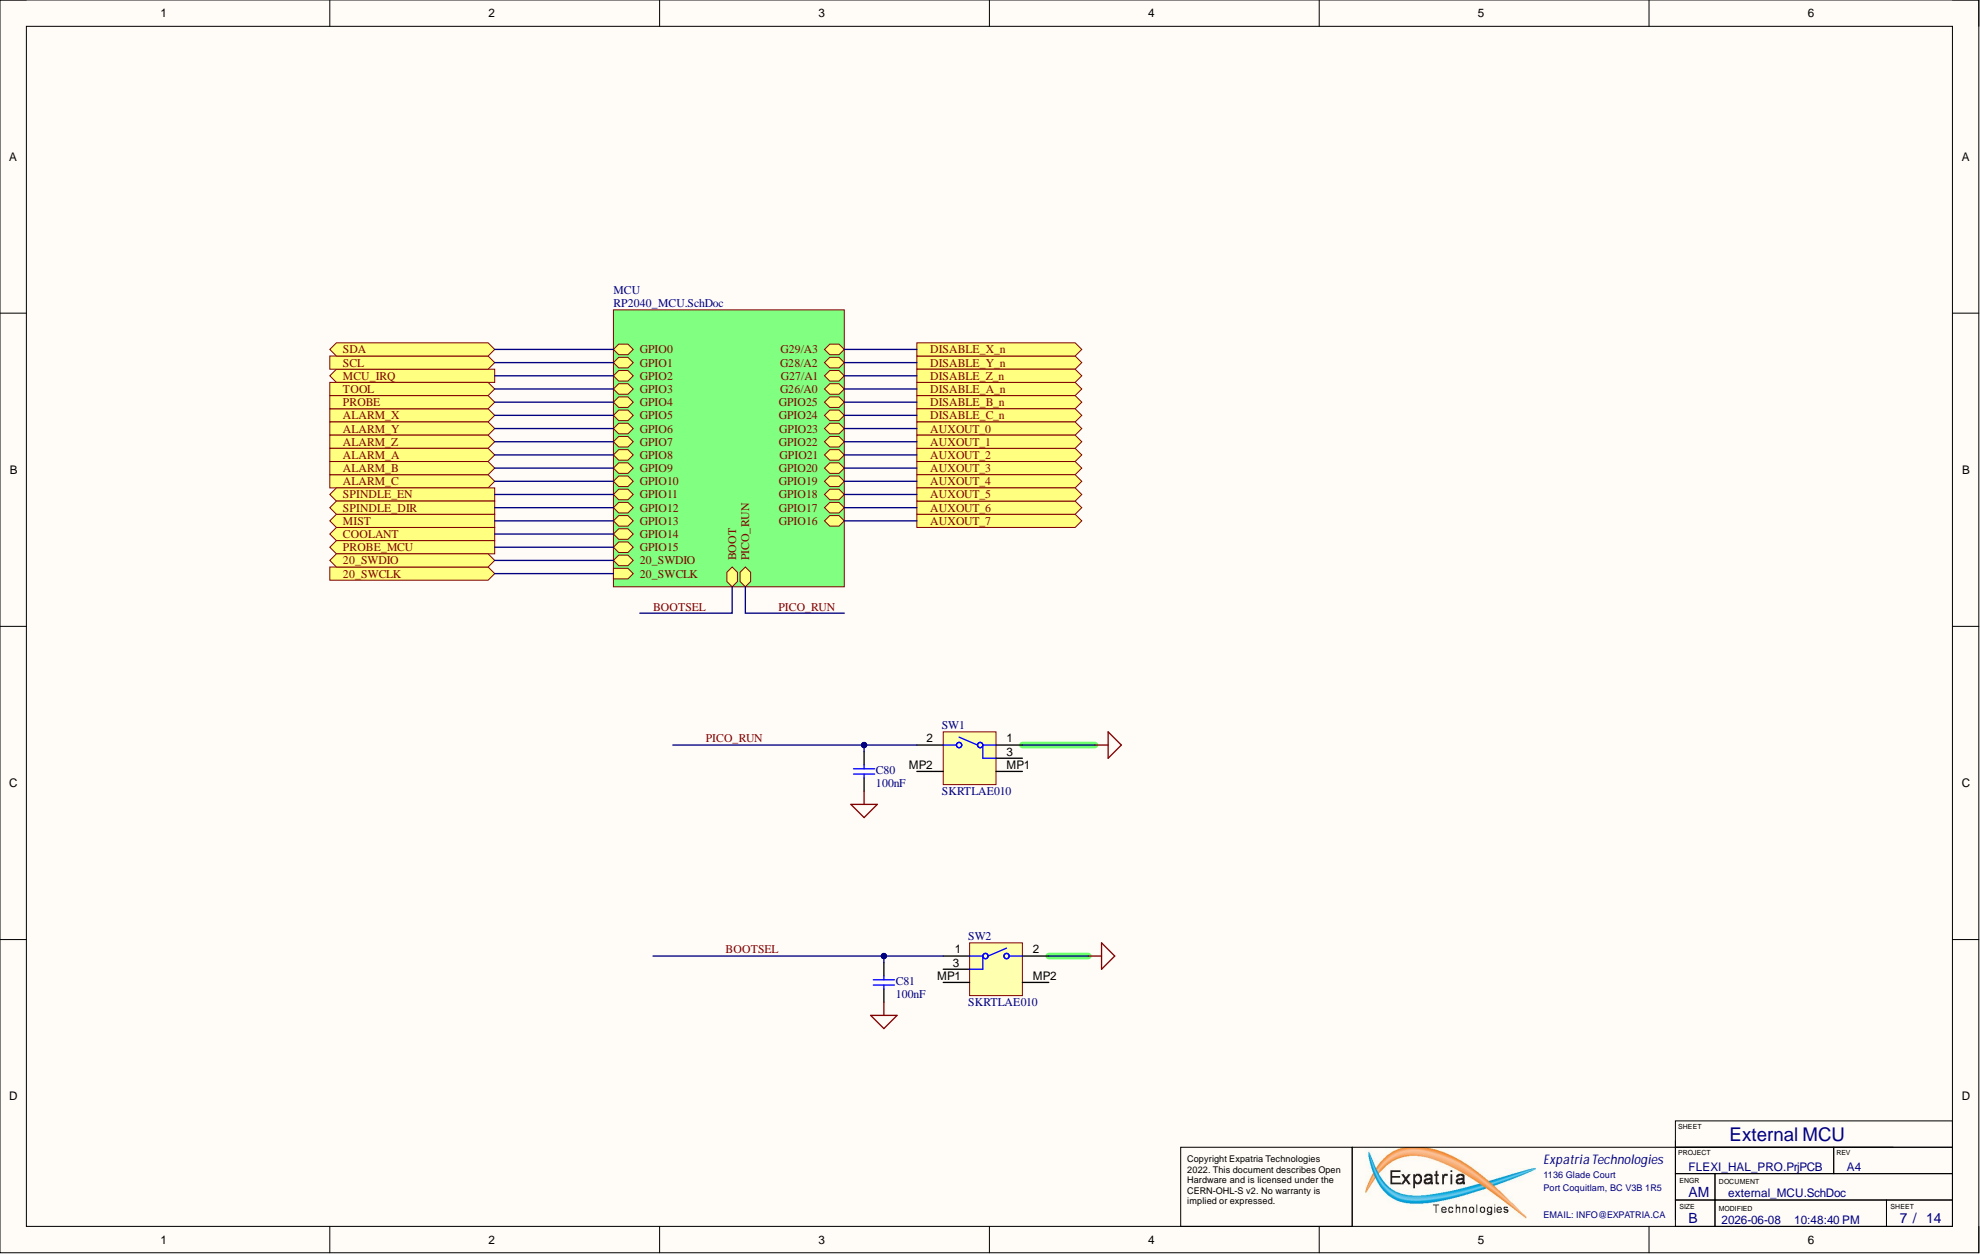
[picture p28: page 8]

external_MCU.SchDoc

Aux_Outputs.SchDoc

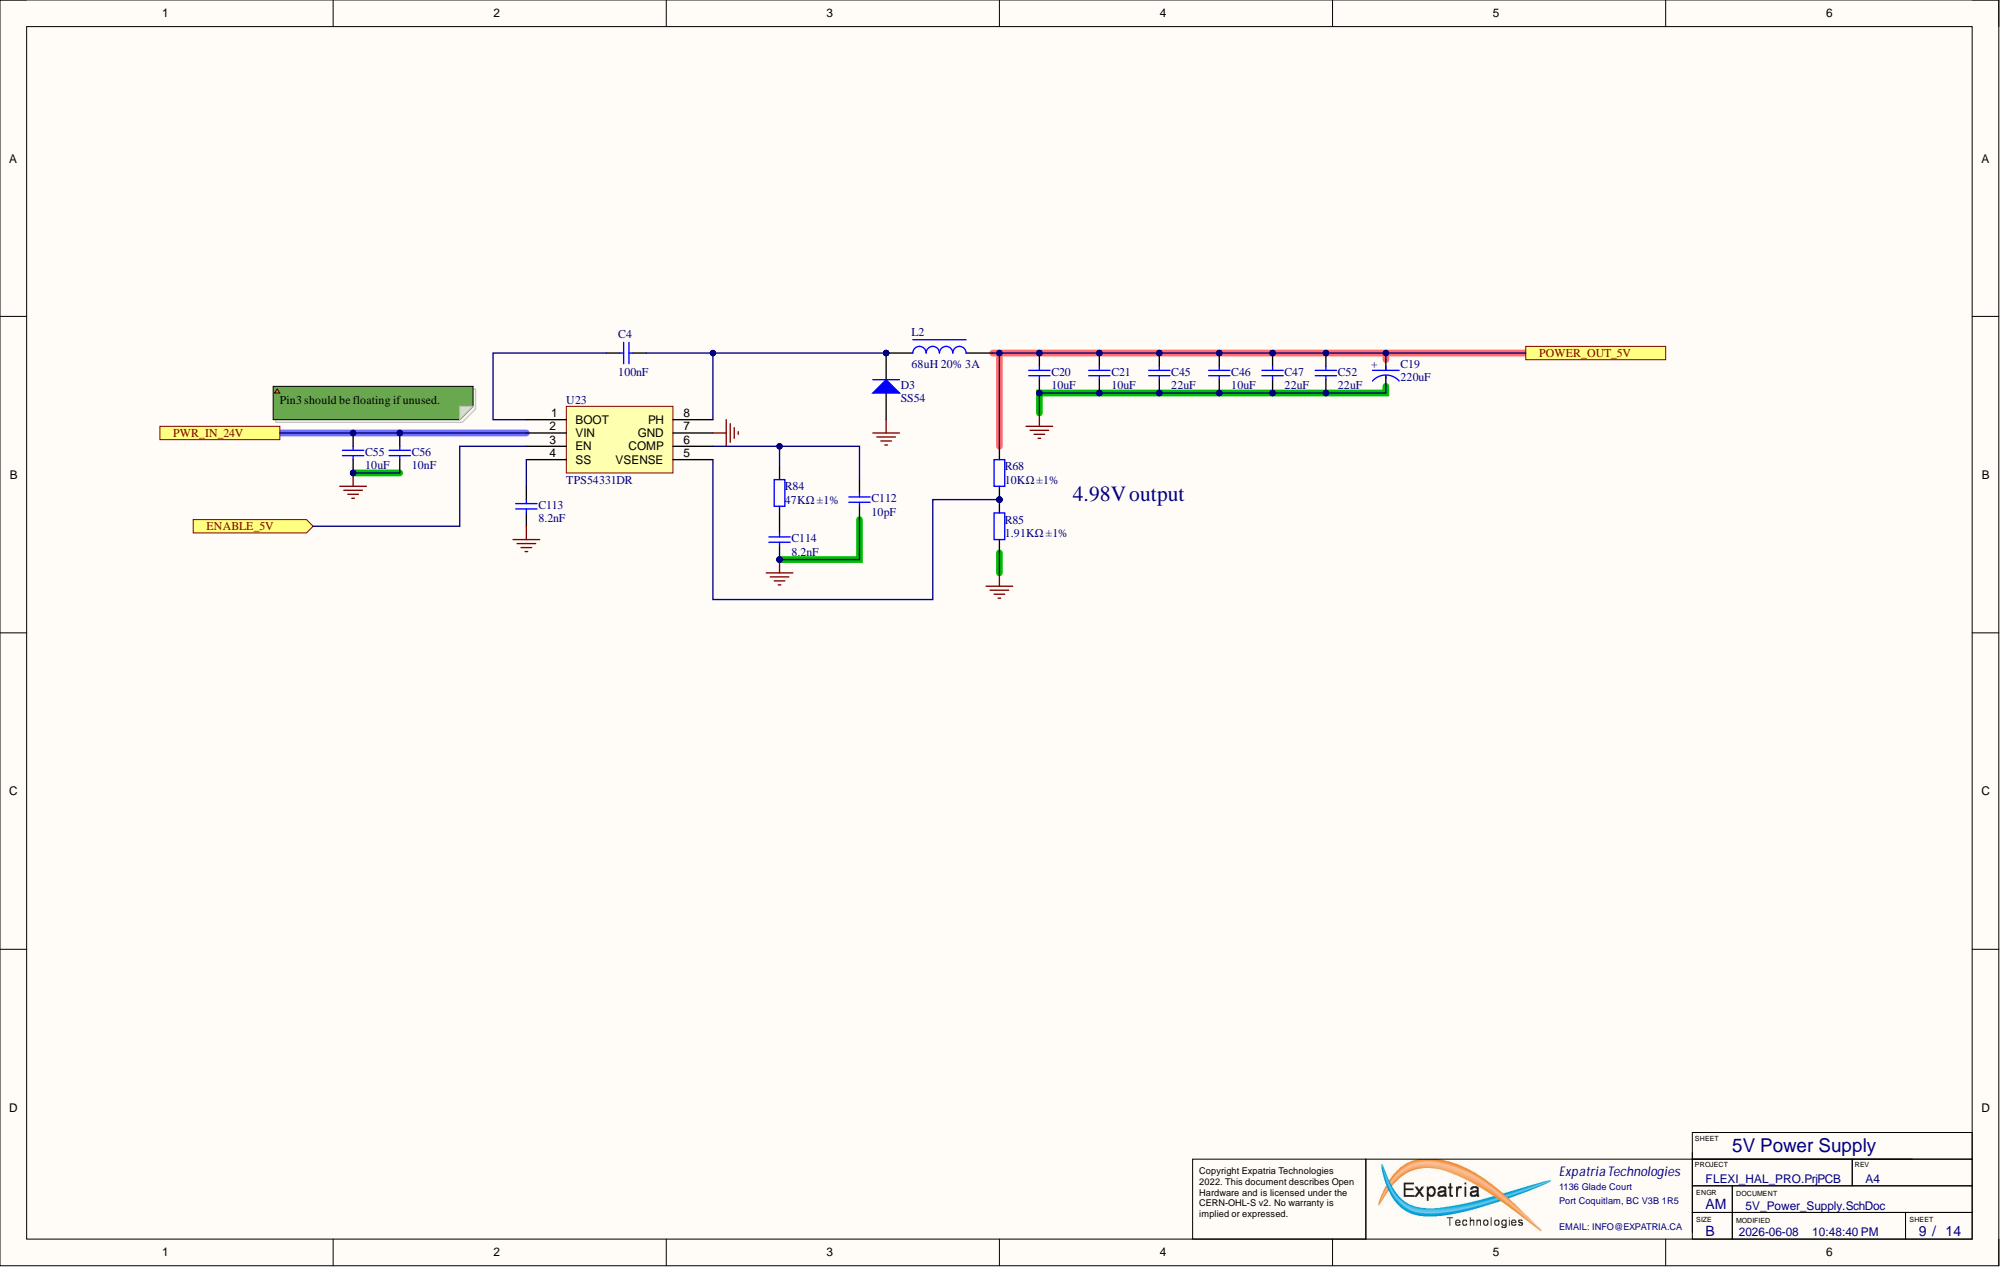
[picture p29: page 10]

Co p yri g ht Ex p atri a Te c h n o l o g i e s 2. Th i s d o c u m e nt d e s cri b e s O p e n Hardware a n d i s l i c e n s e d u n d er th e CERN-OHL-S v 2. No warra nty i s i m p l i e d or e x pre s s e d . | | P R OJE C T FLEXI_HAL_PRO. P rj P C | R E V

E N G R A M | D O C U M E N T 5V_Power_Supply . S c h D o c

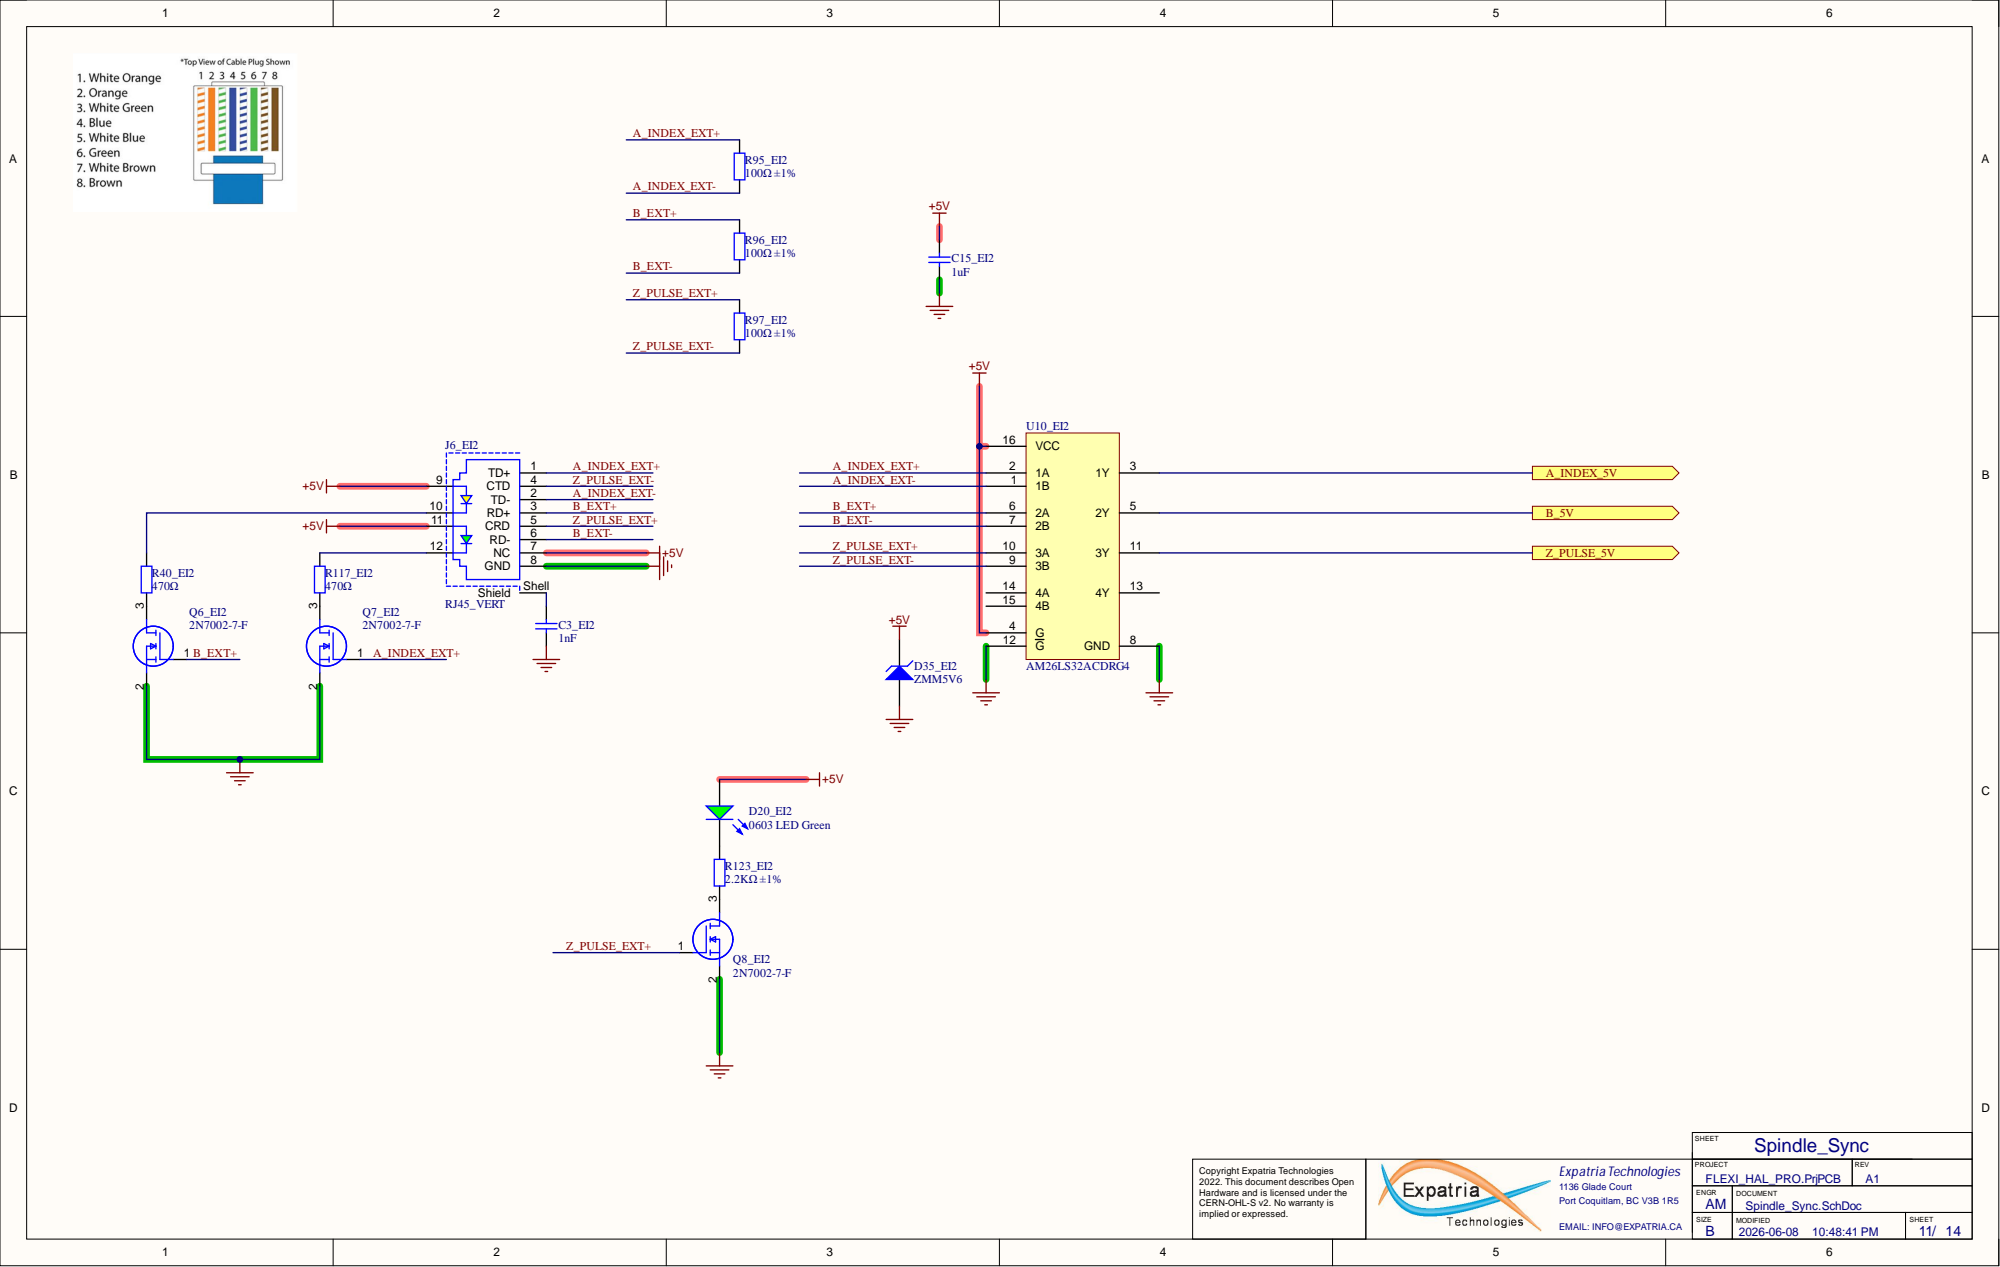
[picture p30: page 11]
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

E N G R A M | D O C U M E N T Spindle_Sync .Sc h D o c

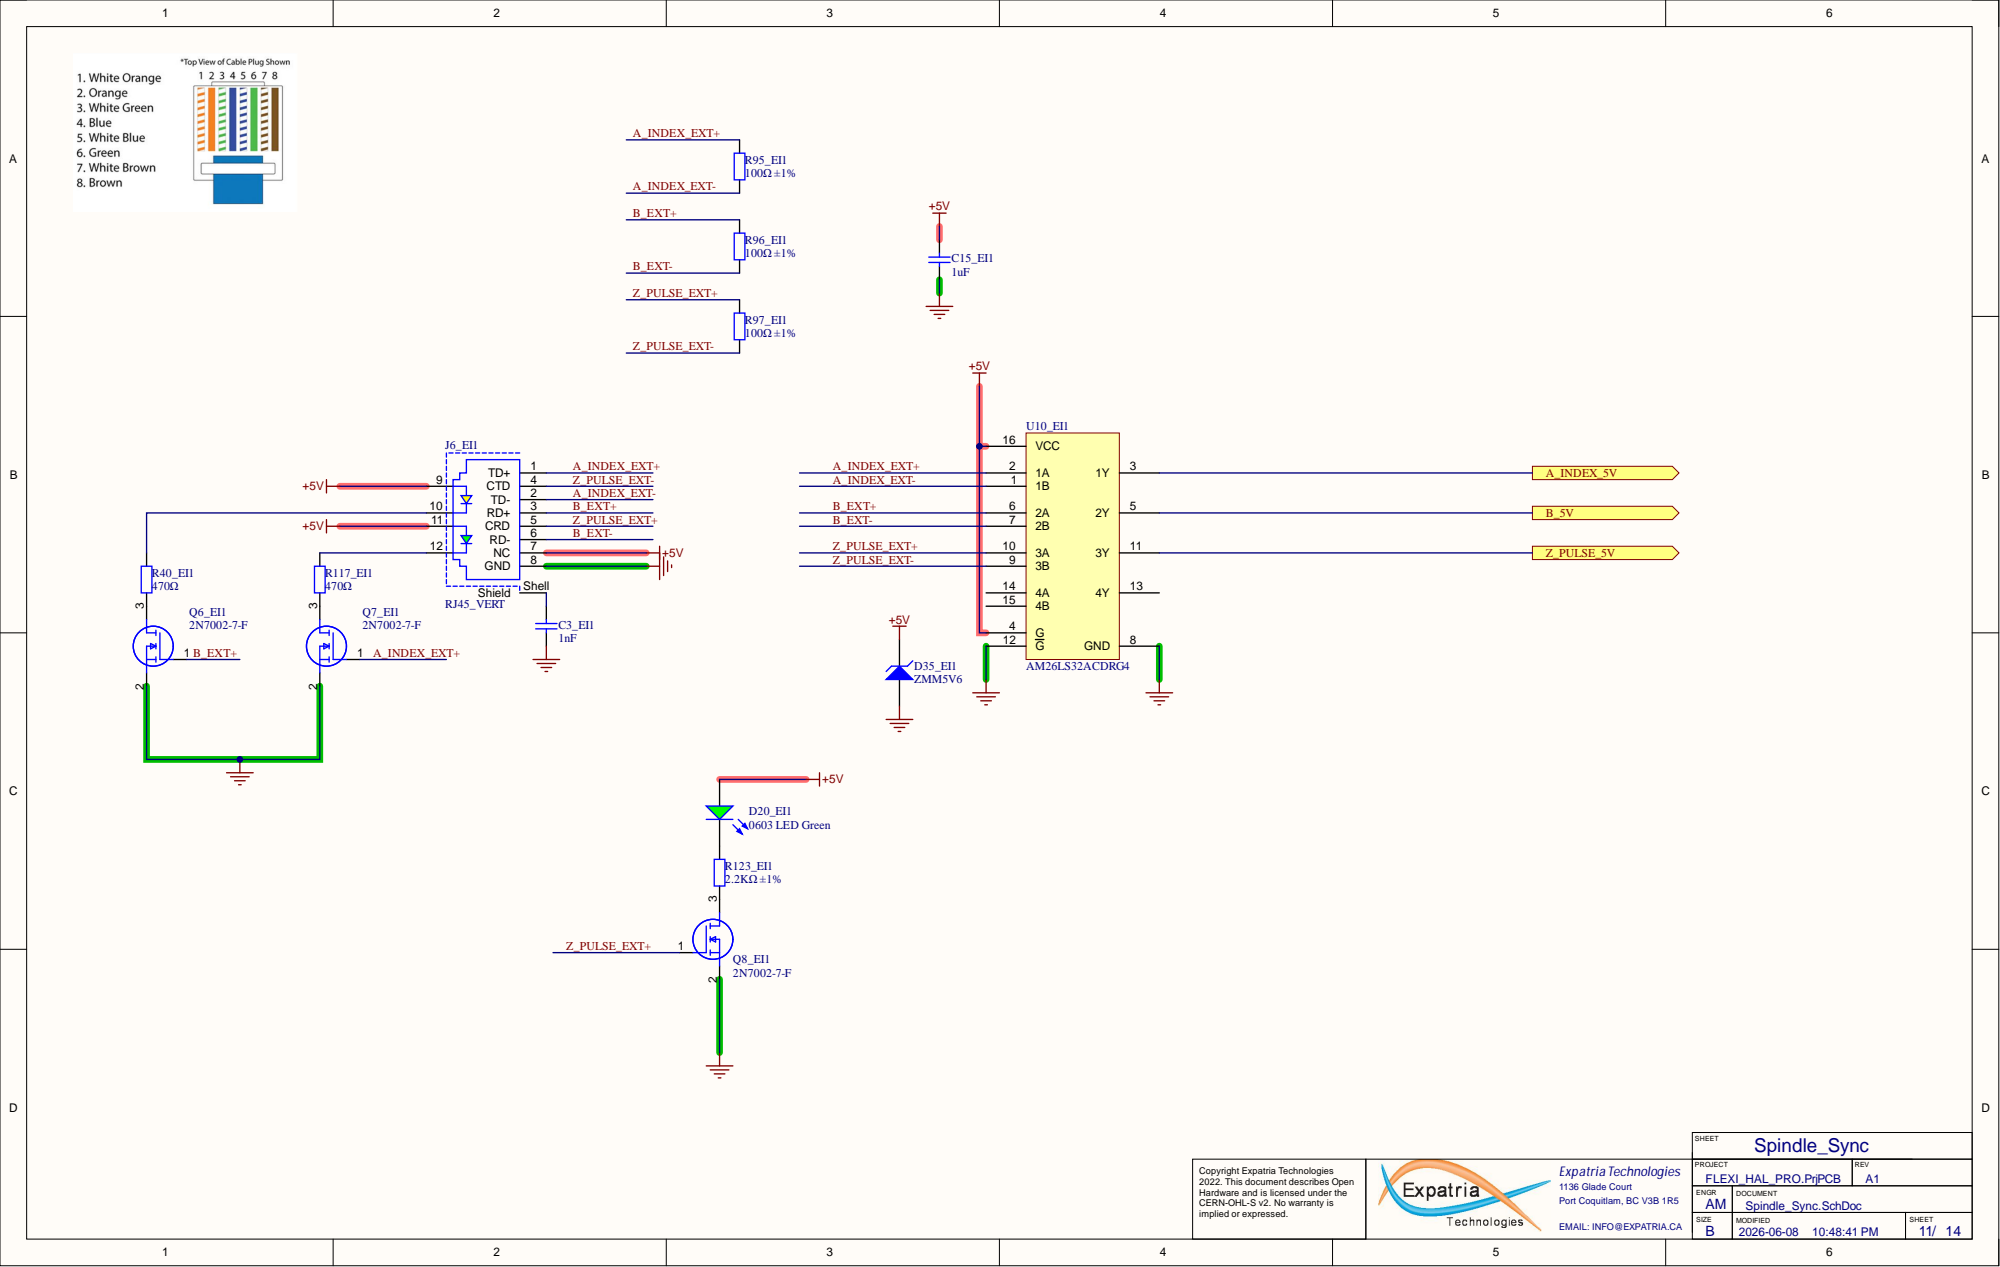
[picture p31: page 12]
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

Pendant is in MCU domain
HALT is active low.

I2C_Keypad.SchDoc

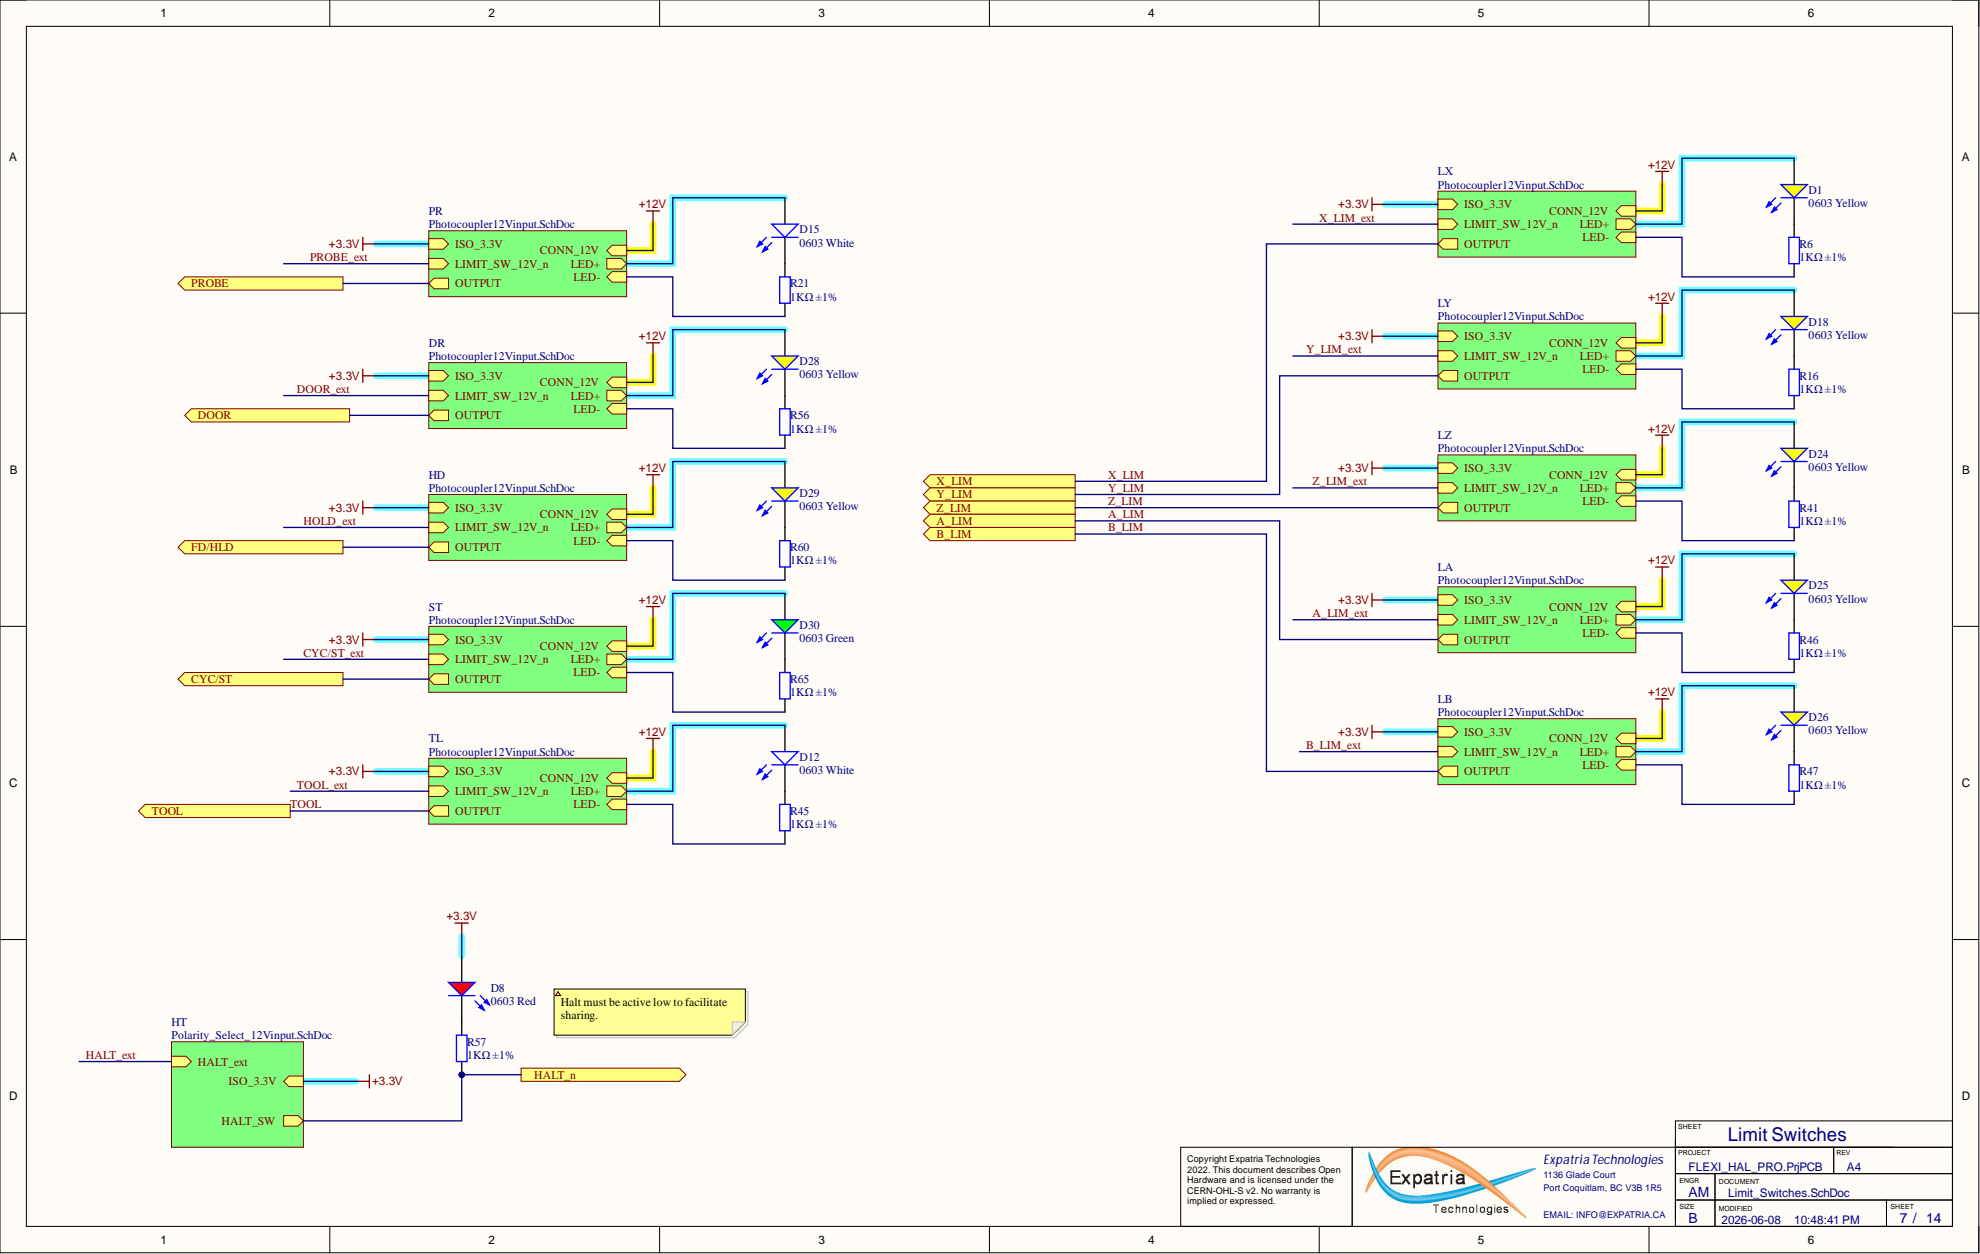
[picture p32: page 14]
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

E N G R A M | D O C U M E N T Limit_Swit ches . S c h D o c

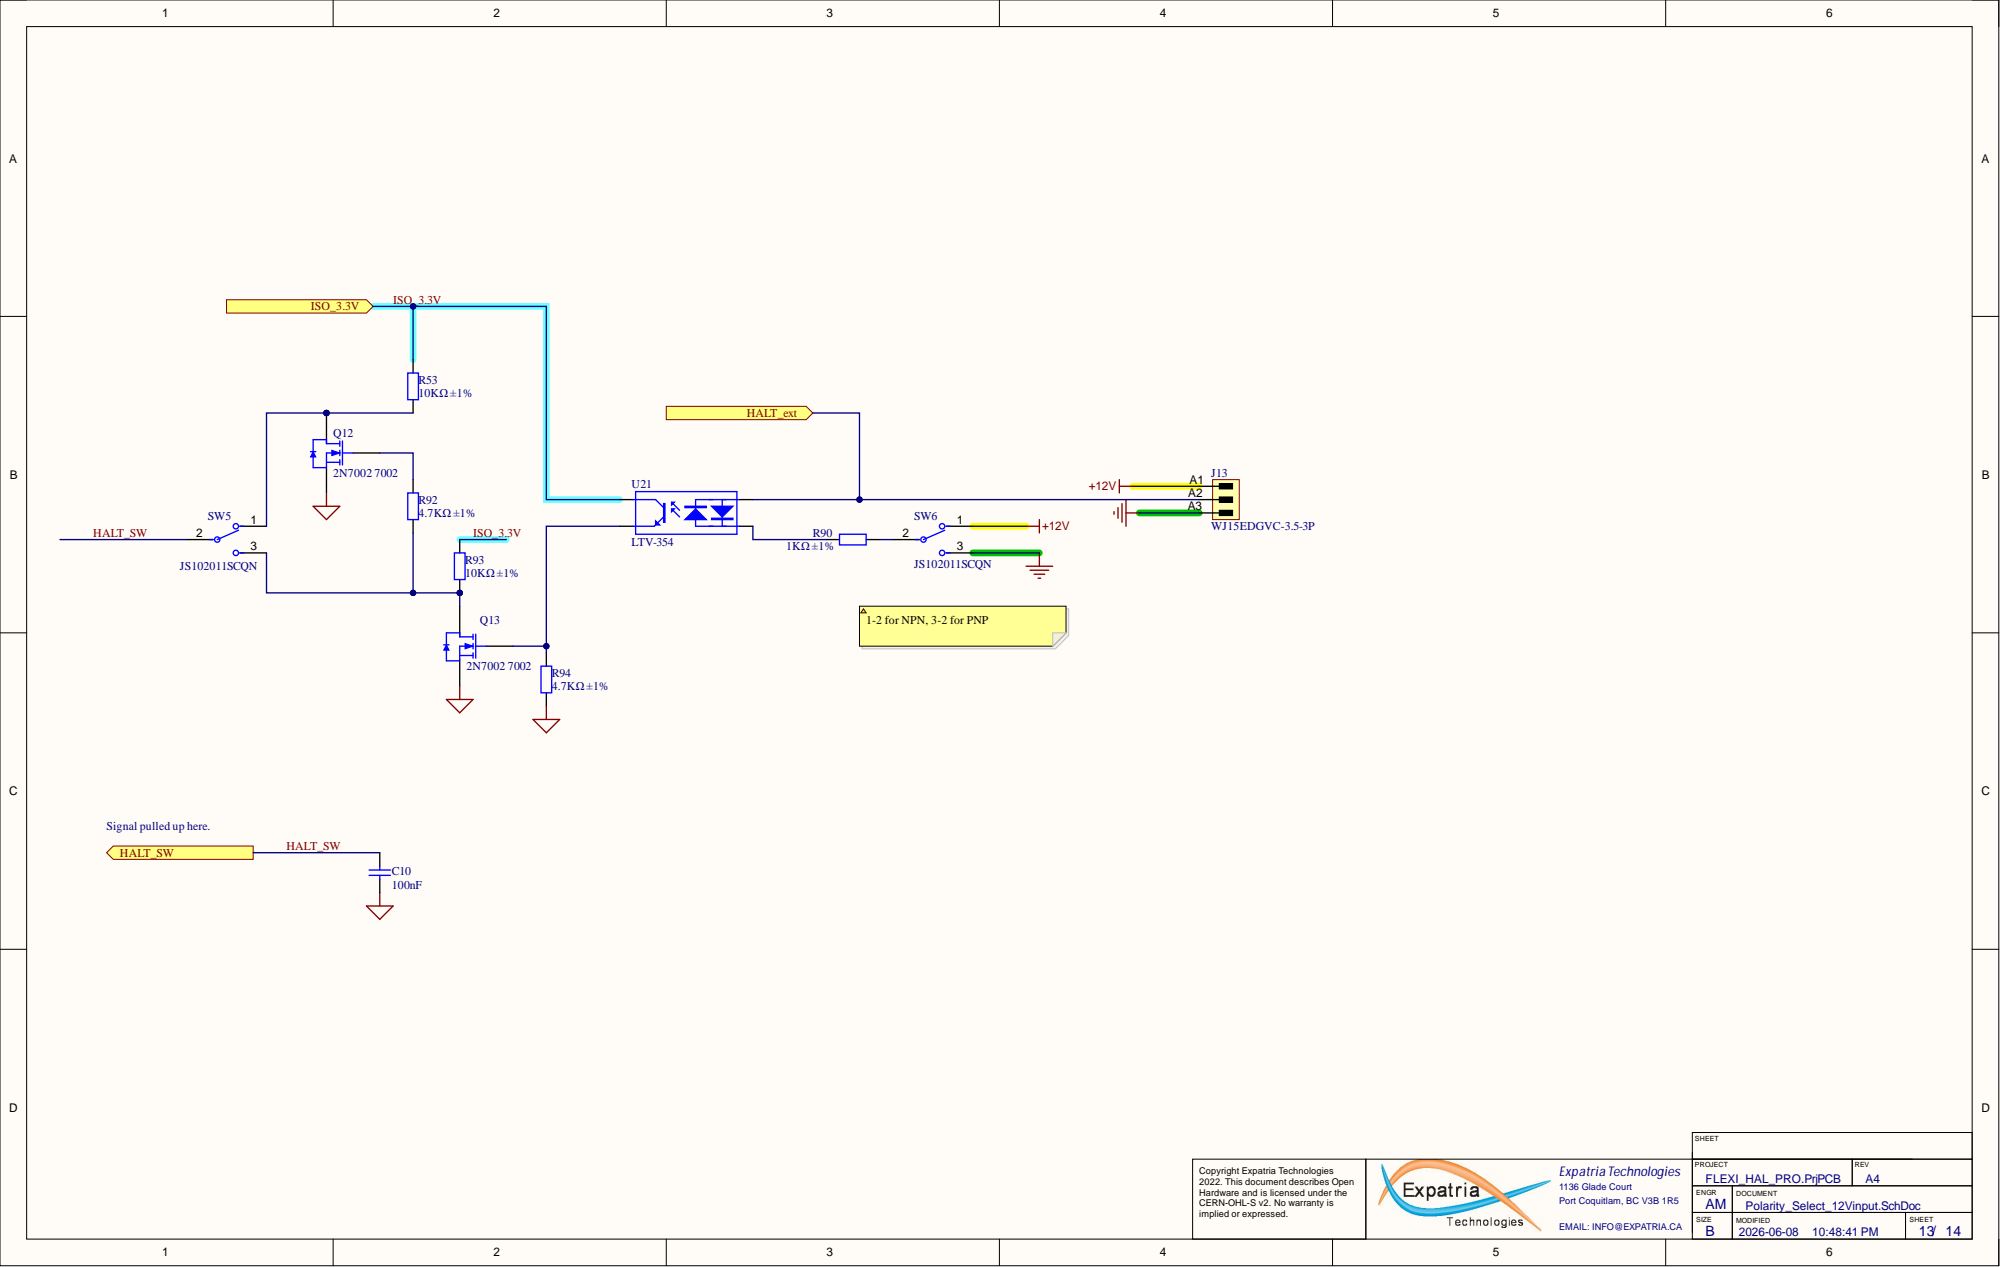
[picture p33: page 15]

1-2 for NPN, 3-2 for PNP

Signal pulled up here.

Polarity_Select_12Vinput.SchDoc


A2
A3

1-2 for NPN, 3-2 for PNP

Photocoupler12Vinput.SchDoc

A2
A3

1-2 for NPN, 3-2 for PNP

Photocoupler12Vinput.SchDoc


A2
A3

1-2 for NPN, 3-2 for PNP

Photocoupler12Vinput.SchDoc


A2
A3

1-2 for NPN, 3-2 for PNP

Photocoupler12Vinput.SchDoc


A2
A3

1-2 for NPN, 3-2 for PNP

Photocoupler12Vinput.SchDoc

A2
A3

1-2 for NPN, 3-2 for PNP

Photocoupler12Vinput.SchDoc


A2
A3

1-2 for NPN, 3-2 for PNP

Photocoupler12Vinput.SchDoc


A2
A3

1-2 for NPN, 3-2 for PNP

Photocoupler12Vinput.SchDoc


A2
A3

1-2 for NPN, 3-2 for PNP

Photocoupler12Vinput.SchDoc

A2
A3

1-2 for NPN, 3-2 for PNP

Photocoupler12Vinput.SchDoc


PO Box 2084
Merritt, BC V1K 1B8
PHONE: (778) 238-9336
EMAIL: info@expatria.ca

Differential_driver.SchDoc


PO Box 2084
Merritt, BC V1K 1B8
PHONE: (778) 238-9336
EMAIL: info@expatria.ca

Differential_driver.SchDoc


PO Box 2084
Merritt, BC V1K 1B8
PHONE: (778) 238-9336
EMAIL: info@expatria.ca

Differential_driver.SchDoc

PO Box 2084
Merritt, BC V1K 1B8
PHONE: (778) 238-9336
EMAIL: info@expatria.ca

Differential_driver.SchDoc


PO Box 2084
Merritt, BC V1K 1B8
PHONE: (778) 238-9336
EMAIL: info@expatria.ca
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
